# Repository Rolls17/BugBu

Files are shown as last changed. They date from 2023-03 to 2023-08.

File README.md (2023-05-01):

# BugBu
Budget Bambu Lab P1P style printer, hence, BugBu. 

Print parts as oriented.  Part description will tell you quantity and if supports are needed.  All parts designed for 0.2mm layer height, 6 walls minimum recommended for strength.

Discord:  https://discord.gg/kHFhCXZnxb

Preview:  https://www.youtube.com/watch?v=aXq7XMQ8wdc

Introduction:  https://www.youtube.com/watch?v=87gVqnMzinw

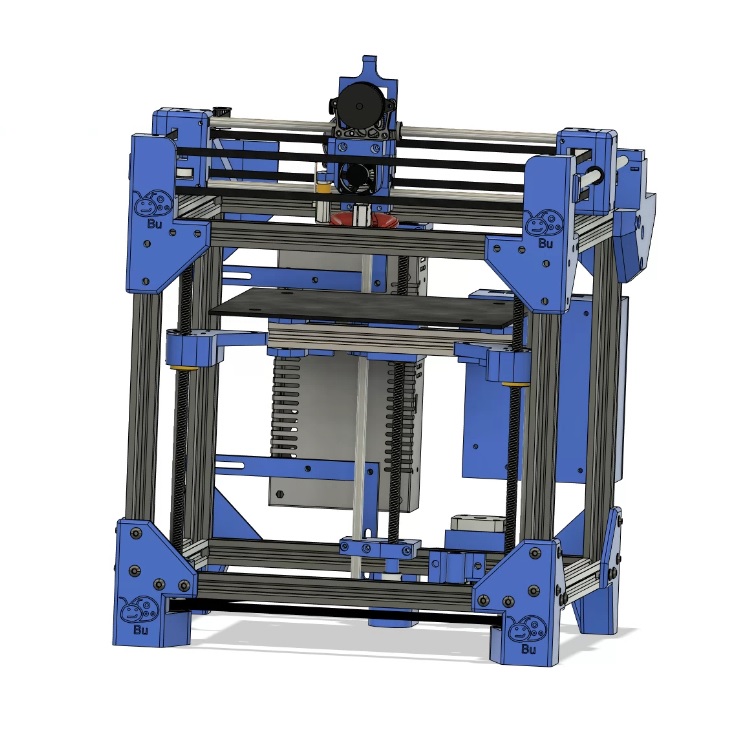
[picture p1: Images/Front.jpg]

Alt text BugBu © 2023 by Royce Rentz is licensed under CC BY-NC 4.0. To view a copy of this license, visit http://creativecommons.org/licenses/by-nc/4.0/

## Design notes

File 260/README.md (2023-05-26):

The BugBu 260 has a printable area of 235x235x300 unless you slap on a Bambu build plate, then you get 260x250x300 build volume.  This uses a cantilever bed to eliminate the closed loop belt system.  All part are printed at 6 walls and 20% infill minimum, designed for 0.4 nozzle at 0.2 layer height.  With lots of testing hours, it is working well currently on the cantilever, but there will be mods coming for it to give a couple of bed operation options.

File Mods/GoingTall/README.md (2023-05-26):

This mod is ONLY for the 310 version of the BugBu. Just replace the same
name parts from the BugBu 310 list with these parts to go tall. You will also
need 2 - MGN12 linear rails for this mod. The linear rails will need to be
50mm shorter than the extrusions you are using for height. For example: If
you order 4 - 500mm extrusions for the height, you would need 2 mgn12
at 450mm. You will also need to use more braces, and be sure your bug is
secured to the table or bench it is on, is it will be top heavy with this mod.
Additional Parts Needed/Deleted from 310 BOM:
ADD - 2 EA: MGN12 linear rails. These will replace 2 linear rods, but you
will still need 1 Linear rod the same length as your Z extrusions. The
MGN12 will need to be 50mm Shorter as noted above
DELETE - 2 EA: Linear Rods for the Z and Linear Bearings for the Z
All other parts in the 310 BOM will remain the same.

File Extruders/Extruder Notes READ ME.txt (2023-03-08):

My current design is standard for the Sherpa Mini mount.  The following are the extruder I can confirm work with the printer.

Sherpa Mini: https://github.com/Annex-Engineering/Sherpa_Mini-Extruder
Print the STL's within the github and follow assembly instructions

Vorxtrudort:  https://github.com/nhchiu/VoronMods/tree/main/Extruders/Vorxtrudort
Print the STL's within the github, BE SURE to print the Sherpa Mini Friction Fit body.  Follow assembly instruction on the github

Hummingbird:  https://github.com/nhchiu/VoronMods/tree/main/Extruders/Hummingbird
Print the STL's within the github, you will also need to order the big gear kit from Aliexpress that is linked in the github.  To mount the Hummingbird, there is an adapter plate STL in the Extruder folder on my page that will mount the extruder.  Follow the assembly instruction on the github.

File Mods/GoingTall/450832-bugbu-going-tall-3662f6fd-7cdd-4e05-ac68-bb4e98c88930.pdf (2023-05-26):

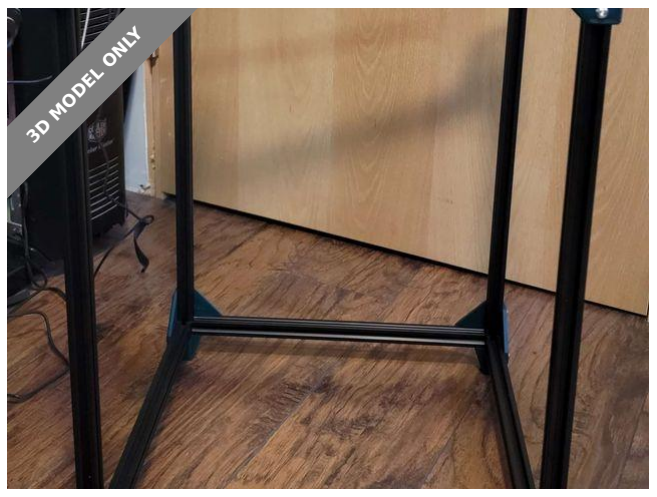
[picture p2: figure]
3D MODEL ONLY

## Summary

This is a mod to allow users to grow the BugBu in height without compromising Z stability

3D Printers (https://printables.com/model?categoryId=1) > 3D Printers - Upgrades (https://printables.com/model?categoryId=2)

Tags: bambu | bugbu | bugbu310 | bugbugoingtall | tallbugbu

This mod is ONLY for the 310 version of the BugBu. Just replace the same name parts from the BugBu 310 list with these parts to go tall. You will also need 2 - MGN12 linear rails for this mod. The linear rails will need to be 50mm shorter than the extrusions you are using for height. For example: If you order 4 - 500mm extrusions for the height, you would need 2 mgn12 at 450mm. You will also need to use more braces, and be sure your bug is secured to the table or bench it is on, is it will be top heavy with this mod.

Additional Parts Needed/Deleted from 310 BOM:

ADD - 2 EA: MGN12 linear rails. These will replace 2 linear rods, but you will still need 1 Linear rod the same length as your Z extrusions. The MGN12 will need to be 50mm Shorter as noted above

DELETE - 2 EA: Linear Rods for the Z and Linear Bearings for the Z

All other parts in the 310 BOM will remain the same.

Rolls17 (https://printables.com/@Rolls17_586768)

## BugBu Going Tall

VIEW IN BROWSER (https://printables.com/model/450832-bugbu-going-tall)

updated 12. 5. 2023 | published 12. 5. 2023

## Model files

fr_bottom_frame_x1.stl

fr_top_x1.stl

fr_bottom_clamp_x1.stl

fl_top_x1.stl

fl_bottom_clamp_x1.stl

fr_top_frame_x1.stl

fl_top_frame_x1.stl

fl_bottom_frame_x1.stl

foot_fr_for_tall_x1.stl

## License

This work is licensed under a
Creative Commons (4.0 International License)

Attribution-NonCommercial (http://creativecommons.org/licenses/by-nc/4.0/)

✖ | Sharing without ATTRIBUTION
✔ | Remix Culture allowed
✖ | Commercial Use
✖ | Free Cultural Works
✖ | Meets Open Definition

idler_fr_for_tall_x1.stl

foot_fl_for_tall_x1.stl

idler_fl_for_tall_x1.stl

310-back-bed-mount-x2-for-using-springs-print-with-… .stl

fr-z-to-bed-for-tall-x1-v1.stl

fl-z-to-bed-for-tall-x1-v1.stl

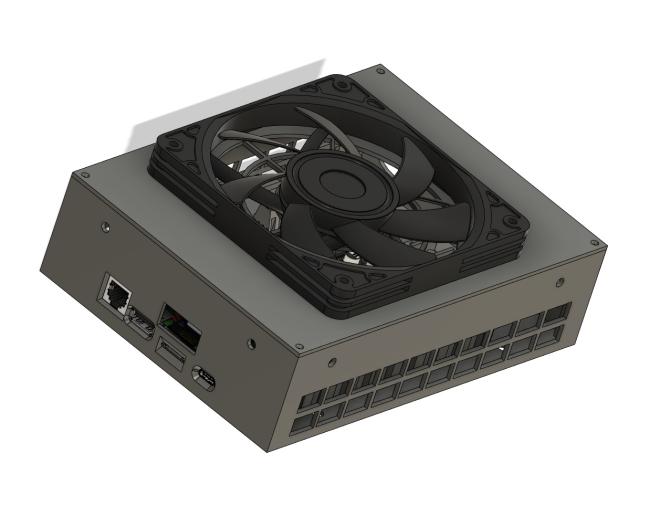
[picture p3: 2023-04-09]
STL Files/Electronics/Octopus/Octopus_Backpack.jpg

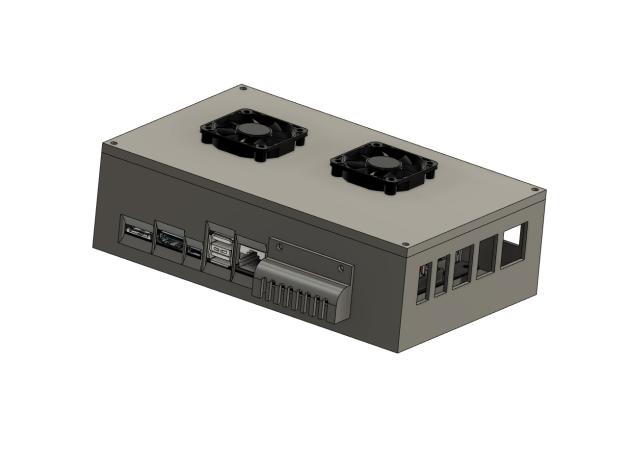
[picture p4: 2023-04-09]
STL Files/Electronics/Manta_M4P/Manta_M4P_Backpack.jpg

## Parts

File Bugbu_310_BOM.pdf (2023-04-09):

MOTION: | Quantity | Price Each | Total | Amazon or Ali Link to Suggested Part
GT2 6mm Belt, 5 meter minimum length | 1 | $9.00 | $9.00
| | | | https://www.amazon.com/dp/B097T212B9/ref=twister_B09877BH12?_e ncoding=UTF8&psc=1
GT2 20 Toothless 5mm bore idler | 10 | $1.20 | $12.00 Printer/dp/B07RV2T54M/ref=sr_1_3?crid=OFZKSAD0WYW1&keywords=g
GT2 20 Tooth 5mm bore timing pulley | 2 | $4.50 | $9.00

https://www.amazon.com/WINSINN-Aluminum-Timing-Pulley-Printer/dp/B07BPGYX3G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

GT2 20 Tooth 5mm bore stepper timing pulley | 3 | $2.50 | $7.50

https://www.amazon.com/WINSINN-Aluminum-Synchronous-Timing-Printer/dp/B077GNZK3J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

GT2 20 Tooth 8mm bore pulley | 3 | $2.50 | $7.50

https://www.amazon.com/WINSINN-Aluminum-Synchronous-Timing-Printer/dp/B077GMKW1C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

8mm linear rod 400mm | 7 | $7.00 | $49.00

https://www.amazon.com/Linear-Motion-15-748-Hardened-Printer/dp/B08JGD9F5P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

### BugBu 310 BOM (315x300x300 build volume)

Please note: The items listed don't include any extra wiring or a Pi and as with any BOM, there are going to be small miscellaneous parts needed along the way. The scew assortments will hopefully cover a lot of the miscellaneous. For a more rigid gantry, 4 - 45mm Linear Bearings are better, but the shorter ones in the BOM will work fine. This list is only a guide, better pricing may be found elsewhere. While every effort has been made to make this a complete list, and the design easy to assemble, please know this is still a self sourced ground up 3D printer build and will require printed parts, time, and attention to details. All work is done so at your own risk and without any liability to the designer of the project.

The STL file parts are pre orientated for best printing. Print with no less than 6 walls and 20% infill. The STL file name will tell you quantity of each item and if it needs supports, only two parts should need supports. I use Polymaker PLA Pro for the parts unless I enclose the printer, I go to Polymaker ASA or ABS.

Linear Bearings | 10 | $1.00 | $10.00

https://www.amazon.com/LM8UU-Linear-Bearings-Length-Printer/dp/B087WPGQ8T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
spons&psc=1&spLa=ZW5jcnlwdGVkUXVhbGlmaWVyPUEyTjRCSDI0RUNW UjZRJmVuY3J5cHRlZElkPUEwODkyMjYwM0ZZOFVJNkFKUVhLOSZlbmNyeX B0ZWRBZElkPUEwMDMxNjg1MVQxUFVBMTRGRVFaTCZ3aWRnZXROYW1 lPXNwX2F0ZiZhY3Rpb249Y2xpY2tSZWRpcmVjdCZkb05vdExvZ0NsaWNrPX RydWU=
Nema17 42mm stepper motor | 3 | $8.25 | $24.75

https://www.amazon.com/POLISI3D-Printer-Stepper-Stepping-Connector/dp/B08HWGYY9D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

8mm 4-start lead screw 400mm | 3 | $11.00 | $33.00

https://www.amazon.com/400mm%EF%BC%8815-75-Inches%EF%BC%89Tr8x8-Thread-Printer-Machine/dp/B08JPNMWP8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

Closed Loop GT2 6mm belt, 1434mm | 1 | $7.00 | $7.00

https://www.aliexpress.us/item/2251832627424600.html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

608 Bearings 8x22x7 skateboard bearings | 9 | $0.56 | $5.04 https://www.amazon.com/%EF%BC%BB10-Pack%EF%BC%BD-608-Ball-
| | | Bearings/dp/B08XVFSZTF/ref=sr_1_4?crid=1QS8OGIPNR2RK&keywords=6
| | | 08+bearing&qid=1677779566&s=industrial&sprefix=608+bearing%2Cindu
| | | strial%2C174&sr=1-4
| | | $0.00
HARDWARE | | | $0.00
Full fastener cart from Bolt Depot
NOTE: Add all items on the list to your cart. This should be all the fasteners you need ACCEPT the t-
nuts. T-nuts listed below. | 1 | $35.00 | $35.00 https://www.boltdepot.com/cart/208641
M5 T-slot/T-nut (this link is for the twist style, there
is a link below in alternates for spring loaded. Pick
your preference) | 100 | $0.06 | $6.00 https://www.amazon.com/Hulless-Sliding-Fastener-Aluminum-
| | | Accessories/dp/B08NZMVP6N/ref=sr_1_14?keywords=m5+t+nut&qid=16
| | | 76582188&sprefix=m5+t%2Caps%2C237&sr=8-14

2020 aluminum extrusion 400mm 10 pack (t or v slot)
You will need a 10 pack and 4 pack, 12 pieces for
the frame and 1 for the print bed (print bed piece
can be left 400 or cut to 300) | 10 | $4.00 | $40.00 https://www.amazon.com/Aluminum-Extrusion-European-Standard-
| | | Industrial/dp/B0B2P434PD/ref=sr_1_8?crid=2H8WDJUWS4H8K&keyword
| | | s=2020%2Baluminum%2Bextrusion%2B300mm&qid=1676582392&sprefix
| | | =2020%2Baluminum%2Bextrusion%2B300mm%2Caps%2C154&sr=8-
| | | 8&th=1

2020 aluminum extrusion 400mm 4 pack(t or v slot) | 4 | $4.75 | $19.00

https://www.amazon.com/OUYZGIA-Aluminum-Extrusion-Extruded-Building/dp/B0B2N3F8DS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

| | | $0.00

EXTRUDER: Note that my design can accommodate a few designs, select which one you want to use, just note you will need a different gear kit for the
Hummbingbird Extruder | | | $0.00
BMG dual drive extruder kit | 1 | $18.00 | $18.00

https://www.amazon.com/Precision-Printer-Plating-Hardened-Extruder/dp/B097YL3C6J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

3D Printed Sherpa Mini (Print parts and assemble)
Use the STL's and build instructions from the GitHub | 1 | https://github.com/Annex-Engineering/Sherpa_Mini-Extruder

3D Printed Hummingbird (Print parts and assemble.
Order big gear kit from Github link) Use the STL's
and build instructions from the GitHub https://github.com/nhchiu/VoronMods/tree/main/Extruders/Hummingbi rd
| | | $0.00
HEATED BED | | | $0.00
Standard ender CR-10 310x310 24v bed | 1 | $42.00 | $42.00

https://www.amazon.com/310x310mm-Aluminum-HeatBed-Thickness-Creality/dp/B07H8DXVQD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

310x310 Build Sheet | 1 | $26.00 | $26.00

https://www.amazon.com/dp/B09M3N2FVS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
| | | $0.00
ELECTRONICS | | | $0.00
3D Touch | 1 | $16.00 | $16.00

https://www.amazon.com/3Dman-Upgrade-Leveling-Sensor-Printers/dp/B08SK62RMR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

24v Power Supply | 1 | $24.00 | $24.00

https://www.amazon.com/ALITOVE-Universal-Regulated-Switching-Transformer/dp/B06XK2ZNKC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 prefix=24v+%2Caps%2C461&sr=1-1-5985efba-8948-4f09-9122-d605505c9d1e

BTT E3 V2/V3 or MKS Robin E3 v1.1 | 1 | $40.00 | $40.00

https://www.amazon.com/BIGTREETECH-Upgrade-Control-TMC2209-Creality/dp/B0882QGFZR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
spons&psc=1&spLa=ZW5jcnlwdGVkUXVhbGlmaWVyPUFQWDA4RVRFNFh GR00mZW5jcnlwdGVkSWQ9QTAwMTk0OTROOFdVWVhEWDdBRjcmZW5 jcnlwdGVkQWRJZD1BMDA2MjM2MTFLUVE1UzUwVU5GUlMmd2lkZ2V0T mFtZT1zcF9hdGYmYWN0aW9uPWNsaWNrUmVkaXJlY3QmZG9Ob3RMb2 dDbGljaz10cnVl
Triangle-lab CHC hotend
The link gives you the option of either standard or
volcano for $5 more, the volcano is recommended
over the standard | 1 | $35.00 | $35.00

https://west3d.com/products/chc-ceramic-heater-core-hot-end-kit-v6-and-volcano-variants-pro

Nema 14 Pancake Stepper | 1 | $22.00 | $22.00

https://www.amazon.com/FYSETC-Printer-Extruder-47-2inch-Accessories/dp/B099JMJNH2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

3010 24v Fan | 1 | $9.00 | $9.00

https://www.amazon.com/HKWANTAT-Bearings-Brushless-Cooling-30x30x10mm/dp/B09MCJ2XSP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

5015 24v Fan | 1 | $9.00 | $9.00

https://www.amazon.com/Brushless-Hydraulic-50mmx50mmx15mm-Appliances-Replacement/dp/B0BBZPB4DM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

Fan wire extensions | 2 | $5.50 | $11.00

https://www.amazon.com/REIFENG-Printer-Cooling-Extension-Connection/dp/B09BN5X6ZT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

Power Switch | 1 | $8.00 | $8.00

https://www.amazon.com/dp/B07KS2TQ45?ref=ppx_yo2ov_dt_b_product_details&th=1
| | | $533.79

## Alternate parts and upgrades

Spring Loaded t-nuts

https://www.amazon.com/Rierdge-European-Standard-Aluminum-Extrusion/dp/B09B3H8RJP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

Pre-assembled Sherpa Mini with stepper motor https://www.amazon.com/FYSETC-Sherpa-Extruder-Compatible-Printer/dp/B095WFBGL4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

BTT BLTouch

https://www.amazon.com/BIGTREETECH-BLTouch-Leveling-Extension-Upgrade/dp/B087CQ3RLG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

Creality CRTouch

https://www.amazon.com/gp/product/B09XCGPLXH/ref=ewc_pr_img_1?smid=A113EI13J39RO4&psc=1

## Individual fastener list in case you need to source from elsewhere

M3, M4, M5 Nut and Screw Kit | 1 | $15.00

https://www.amazon.com/Hilitchi-510-Pcs-Socket-Screws-Assortment/dp/B073SWXPYR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
0186dd22447b&pd_rd_w=jmPHz&pd_rd_wg=kQ31h&pf_rd_p=8f2bf95d-b9c2-4e6d-96a9-
5fdf77a1951d&pf_rd_r=RBMRTG4MGTVCWFG3QMHH&qid=1677710013 &sprefix=M3+M4+M%2Caps%2C158&sr=1-1-270ce31b-afa8-499f-878b-3bb461a9a5a6
M3 longer fastener kit | 1 | $9.28

https://www.amazon.com/iexcell-Metric-M5-0-8-Stainless-Assortment/dp/B08GZWVN4D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

M5 longer fastener kit | 1 | $9.80

https://www.amazon.com/iexcell-Metric-M5-0-8-Stainless-Assortment/dp/B07HDL3KVG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

Assorted M3 Kit | 1 | $12.00

https://www.amazon.com/Kadrick-Bolts%EF%BC%8CFlat-Washers-Assortment-Stainless/dp/B0BPFWBBF9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 N00mZW5jcnlwdGVkSWQ9QTA0MzU1MDgzSVdTSUdRRlQ2NVBOJmVuY3 J5cHRlZEFkSWQ9QTAwMjM5ODcxT0pGTURMRUdQSUZXJndpZGdldE5hb WU9c3BfYXRmJmFjdGlvbj1jbGlja1JlZGlyZWN0JmRvTm90TG9nQ2xpY2s9d HJ1ZQ==

M4x50 countersunk flat head | 4 | $2.00

https://www.amazon.com/METALLIXITY-Countersunk-Machine-M4x30mm-Stainless/dp/B09Y5P7X75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

M5x12 (M5x10 works too) button head | 100 | $0.10

https://www.amazon.com/M5-0-8-Button-Socket-Stainless-Quantity/dp/B07NVJT9VB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 R0tNJmVuY3J5cHRlZElkPUEwNjE3MjQyNFBaWERJNkJaNFZCJmVuY3J5cHR lZEFkSWQ9QTAxMTk0NzMxTjlKWDg1SDVHN1NaJndpZGdldE5hbWU9c3Bf YXRmJmFjdGlvbj1jbGlja1JlZGlyZWN0JmRvTm90TG9nQ2xpY2s9dHJ1ZQ==

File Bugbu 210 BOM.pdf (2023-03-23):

MOTION: | Quantity | Price Each | Total | Amazon or Ali Link to Suggested Part
GT2 6mm Belt, 5 meter minimum length | 1 | $9.00 | $9.00
| | | | https://www.amazon.com/dp/B097T212B9/ref=twister_B09877BH12?_e ncoding=UTF8&psc=1
GT2 20 Toothless 5mm bore idler | 10 | $1.20 | $12.00 Printer/dp/B07RV2T54M/ref=sr_1_3?crid=OFZKSAD0WYW1&keywords=g
GT2 20 Tooth 5mm bore timing pulley | 2 | $4.50 | $9.00

https://www.amazon.com/WINSINN-Aluminum-Timing-Pulley-Printer/dp/B07BPGYX3G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

GT2 20 Tooth 5mm bore stepper timing pulley | 3 | $2.50 | $7.50

https://www.amazon.com/WINSINN-Aluminum-Synchronous-Timing-Printer/dp/B077GNZK3J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

GT2 20 Tooth 8mm bore pulley | 3 | $2.50 | $7.50

https://www.amazon.com/WINSINN-Aluminum-Synchronous-Timing-Printer/dp/B077GMKW1C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

8mm linear rod 300mm | 7 | $5.25 | $36.75

https://www.amazon.com/300mm-Linear-Motion-Printer-Machine/dp/B09P87MSY7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

### BugBu 300 BOM (215x200x200 build volume)

Please note: The items listed don't include any extra wiring or a Pi and as with any BOM, there are going to be small miscellaneous parts needed along the way. The scew assortments will hopefully cover a lot of the miscellaneous. For a more rigid gantry, 4 - 45mm Linear Bearings are better, but the shorter ones in the BOM will work fine. This list is only a guide, better pricing may be found elsewhere. While every effort has been made to make this a complete list, and the design easy to assemble, please know this is still a self sourced ground up 3D printer build and will require printed parts, time, and attention to details. All work is done so at your own risk and without any liability to the designer of the project.

The STL file parts are pre orientated for best printing. Print with no less than 6 walls and 20% infill. The STL file name will tell you quantity of each item and if it needs supports, only two parts should need supports. I use Polymaker PLA Pro for the parts unless I enclose the printer, I go to Polymaker ASA or ABS.

Linear Bearings | 10 | $1.00 | $10.00

https://www.amazon.com/LM8UU-Linear-Bearings-Length-Printer/dp/B087WPGQ8T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
spons&psc=1&spLa=ZW5jcnlwdGVkUXVhbGlmaWVyPUEyTjRCSDI0RUNW UjZRJmVuY3J5cHRlZElkPUEwODkyMjYwM0ZZOFVJNkFKUVhLOSZlbmNyeX B0ZWRBZElkPUEwMDMxNjg1MVQxUFVBMTRGRVFaTCZ3aWRnZXROYW1 lPXNwX2F0ZiZhY3Rpb249Y2xpY2tSZWRpcmVjdCZkb05vdExvZ0NsaWNrPX RydWU=
Nema17 42mm stepper motor | 3 | $8.25 | $24.75

https://www.amazon.com/POLISI3D-Printer-Stepper-Stepping-Connector/dp/B08HWGYY9D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

8mm 4-start lead screw 300mm | 3 | $7.00 | $21.00

https://www.amazon.com/ReliaBot-300mm-Thread-Starts-Printer/dp/B0829J9YJ1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

Closed Loop GT2 6mm belt, 1080mm - 1100mm | 1 | $6.50 | $6.50

https://www.aliexpress.us/item/2251832113069399.html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 bd8be16777098448855150d06df%2110000003969762805%21sea%21US %210&curPageLogUid=Sgd0cwKojbJx

608 Bearings 8x22x7 skateboard bearings | 9 | $0.56 | $5.04

https://www.amazon.com/%EF%BC%BB10-Pack%EF%BC%BD-608-Ball-Bearings/dp/B08XVFSZTF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
| | | $0.00
HARDWARE | | | $0.00
M5x12 (M5x10 works too) button head | 100 | $0.10 | $10.00

https://www.amazon.com/M5-0-8-Button-Socket-Stainless-Quantity/dp/B07NVJT9VB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 R0tNJmVuY3J5cHRlZElkPUEwNjE3MjQyNFBaWERJNkJaNFZCJmVuY3J5cHR lZEFkSWQ9QTAxMTk0NzMxTjlKWDg1SDVHN1NaJndpZGdldE5hbWU9c3Bf YXRmJmFjdGlvbj1jbGlja1JlZGlyZWN0JmRvTm90TG9nQ2xpY2s9dHJ1ZQ==

M5 T-slot/T-nut | 100 | $0.06 | $6.00

https://www.amazon.com/Hulless-Sliding-Fastener-Aluminum-Accessories/dp/B08NZMVP6N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

Assorted M3 Kit | 1 | $12.00 | $12.00

https://www.amazon.com/Kadrick-Bolts%EF%BC%8CFlat-Washers-Assortment-Stainless/dp/B0BPFWBBF9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 N00mZW5jcnlwdGVkSWQ9QTA0MzU1MDgzSVdTSUdRRlQ2NVBOJmVuY3 J5cHRlZEFkSWQ9QTAwMjM5ODcxT0pGTURMRUdQSUZXJndpZGdldE5hb WU9c3BfYXRmJmFjdGlvbj1jbGlja1JlZGlyZWN0JmRvTm90TG9nQ2xpY2s9d HJ1ZQ==

M4x50 countersunk flat head | 4 | $2.00 | $8.00

https://www.amazon.com/METALLIXITY-Countersunk-Machine-M4x30mm-Stainless/dp/B09Y5P7X75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
2020 aluminum extrusion 300mm 10 pack (t or v slot)
You will need a 10 pack and 4 pack, 12 pieces for
the frame and 1 for the print bed (print bed piece
can be left 300 or cut to 200) | 10 | $3.25 | $32.50

https://www.amazon.com/Aluminum-Extrusion-European-Standard-Industrial/dp/B0B2PBF6YB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

2020 aluminum extrusion 300mm 4 pack(t or v slot) | 4 | $4.00 | $16.00

https://www.amazon.com/OUYZGIA-Aluminum-Extrusion-Extruded-Building/dp/B0B2N4YY1W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

M3, M4, M5 Nut and Screw Kit | 1 | $15.00 | $15.00

https://www.amazon.com/Hilitchi-510-Pcs-Socket-Screws-Assortment/dp/B073SWXPYR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
0186dd22447b&pd_rd_w=jmPHz&pd_rd_wg=kQ31h&pf_rd_p=8f2bf95d-b9c2-4e6d-96a9-
5fdf77a1951d&pf_rd_r=RBMRTG4MGTVCWFG3QMHH&qid=1677710013 &sprefix=M3+M4+M%2Caps%2C158&sr=1-1-270ce31b-afa8-499f-878b-3bb461a9a5a6

M3 longer fastener kit | 1 | $9.28 | $9.28

https://www.amazon.com/iexcell-Metric-M5-0-8-Stainless-Assortment/dp/B08GZWVN4D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

M5 longer fastener kit | 1 | $9.80 | $9.80

https://www.amazon.com/iexcell-Metric-M5-0-8-Stainless-Assortment/dp/B07HDL3KVG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
| | | $0.00

EXTRUDER: Note that my design can accommodate a few designs, select which one you want to use, just note you will need a different gear kit for the
Hummbingbird Extruder | | | $0.00
BMG dual drive extruder kit | 1 | $18.00 | $18.00

https://www.amazon.com/Precision-Printer-Plating-Hardened-Extruder/dp/B097YL3C6J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

3D Printed Sherpa Mini (Print parts and assemble)
Use the STL's and build instructions from the GitHub | 1 | https://github.com/Annex-Engineering/Sherpa_Mini-Extruder

3D Printed Vorxtrudort (Print parts and assemble)
Use the STL's and build instructions from the GitHub | https://github.com/nhchiu/VoronMods/tree/main/Extruders/Vorxtrudort

3D Printed Hummingbird (Print parts and assemble.
Order big gear kit from Github link) Use the STL's
and build instructions from the GitHub https://github.com/nhchiu/VoronMods/tree/main/Extruders/Hummingbi rd
| | | $0.00
HEATED BED | | | $0.00
Standard ender 3 235x235 24v bed | 1 | $25.00 | $25.00

https://www.amazon.com/Ender-V2-Heated-Bed-Replacement/dp/B08VHTW8CQ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
spons&psc=1&spLa=ZW5jcnlwdGVkUXVhbGlmaWVyPUExQjRXTFBEVzlON 0ZIJmVuY3J5cHRlZElkPUEwODY2MjI3MjhIVkxDODZEUUk4UyZlbmNyeXB0 ZWRBZElkPUEwMzMxNDM0M1RBNkM2UDRIV01IWCZ3aWRnZXROYW1lP XNwX2F0ZiZhY3Rpb249Y2xpY2tSZWRpcmVjdCZkb05vdExvZ0NsaWNrPXRy dWU=

235x235 build sheet | 1 | $12.00 | $12.00

https://www.amazon.com/dp/B0856VT5XT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
| | | $0.00
ELECTRONICS | | | $0.00
3D Touch | 1 | $16.00 | $16.00

https://www.amazon.com/3Dman-Upgrade-Leveling-Sensor-Printers/dp/B08SK62RMR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

24v Power Supply | 1 | $24.00 | $24.00

https://www.amazon.com/ALITOVE-Universal-Regulated-Switching-Transformer/dp/B06XK2ZNKC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 prefix=24v+%2Caps%2C461&sr=1-1-5985efba-8948-4f09-9122-d605505c9d1e

BTT E3 V2/V3 or MKS Robin E3 v1.1 | 1 | $40.00 | $40.00

https://www.amazon.com/BIGTREETECH-Upgrade-Control-TMC2209-Creality/dp/B0882QGFZR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
spons&psc=1&spLa=ZW5jcnlwdGVkUXVhbGlmaWVyPUFQWDA4RVRFNFh GR00mZW5jcnlwdGVkSWQ9QTAwMTk0OTROOFdVWVhEWDdBRjcmZW5 jcnlwdGVkQWRJZD1BMDA2MjM2MTFLUVE1UzUwVU5GUlMmd2lkZ2V0T mFtZT1zcF9hdGYmYWN0aW9uPWNsaWNrUmVkaXJlY3QmZG9Ob3RMb2 dDbGljaz10cnVl

Triangle-lab CHC hotend | 1 | $31.00 | $31.00

https://www.aliexpress.us/item/3256803662839179.html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 00bb6416777106954414139d0729%2112000027332429742%21sea%21U S%210&curPageLogUid=cpJxAMdvL2Ar

Nema 14 Pancake Stepper | 1 | $22.00 | $22.00

https://www.amazon.com/FYSETC-Printer-Extruder-47-2inch-Accessories/dp/B099JMJNH2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

3010 24v Fan | 1 | $9.00 | $9.00

https://www.amazon.com/HKWANTAT-Bearings-Brushless-Cooling-30x30x10mm/dp/B09MCJ2XSP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

5015 24v Fan | 1 | $9.00 | $9.00

https://www.amazon.com/Brushless-Hydraulic-50mmx50mmx15mm-Appliances-Replacement/dp/B0BBZPB4DM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

Power Switch | 1 | $8.00 | $8.00

https://www.amazon.com/dp/B07KS2TQ45?ref=ppx_yo2ov_dt_b_product_details&th=1
| | | $481.62

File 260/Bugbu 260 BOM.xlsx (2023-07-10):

BugBu 260 BOM (Acheivable 260x250x300 build volume) This build uses the Ender 3 24v Heated Bed. You can either use the full 235x235 bed area with space around it, or get a Bambu build plate to get a 260x250 print bed area
Please note: The items listed don't include any extra wiring or a Pi and as with any BOM, there are going to be small miscellaneous parts needed along the way. The scew assortments will hopefully cover a lot of the miscellaneous. For a more rigid gantry, 4 - 45mm Linear Bearings are better, but the shorter ones in the BOM will work fine. This list is only a guide, better pricing may be found elsewhere. While every effort has been made to make this a complete list, and the design easy to assemble, please know this is still a self sourced ground up 3D printer build and will require printed parts, time, and attention to details. All work is done so at your own risk and without any liability to the designer of the project. The STL file parts are pre orientated for best printing. Print with no less than 6 walls and 20% infill. The STL file name will tell you quantity of each item and if it needs supports, only two parts should need supports. I use Polymaker PLA Pro for the parts unless I enclose the printer, I go to Polymaker ASA or ABS.
MOTION: | Quantity | Price Each | Total | Amazon or Ali Link to Suggested Part
GT2 6mm Belt, 5 meter minimum length | 1 | $9.00 | $9.00 | https://www.amazon.com/dp/B097T212B9/ref=twister_B09877BH12?_encoding=UTF8&psc=1
GT2 20 Toothless 5mm bore idler | 7 | $1.75 | $12.25 | https://www.amazon.com/3Dman-Toothless-Aluminum-Timing-Printer/dp/B07RV2T54M
GT2 20 Tooth 5mm bore timing pulley | 2 | $4.50 | $9.00 | https://www.amazon.com/WINSINN-Aluminum-Timing-Pulley-Printer/dp/B07BPGYX3G
GT2 20 Tooth 5mm bore stepper timing pulley | 3 | $2.50 | $7.50 | https://www.amazon.com/WINSINN-Aluminum-Synchronous-Timing-Printer/dp/B077GNZK3J
8mm linear rod 350mm | 4 | $4.50 | $18.00 | https://www.amazon.com/300mm-Linear-Motion-Printer-Machine/dp/B09P86HCNM
Linear Bearings (these are 45mm bearings and much smoother than the cheap 10 pack) | 4 | $4.00 | $16.00 | https://www.amazon.com/Printer-Bearings-JGAurora-LM08LUU-LM8LUU/dp/B083XQTH41
Nema17 42mm stepper motor | 3 | $8.25 | $24.75 | https://www.amazon.com/POLISI3D-Printer-Stepper-Stepping-Connector/dp/B08HWGYY9D
8mm 4-start lead screw 350mm | 1 | $9.50 | $9.50 | https://www.amazon.com/ReliaBot-300mm-Thread-Starts-Printer/dp/B078R7XJP3
MGN12H Linear Rail | 2 | $19.00 | $38.00 | https://www.amazon.com/dp/B0B1LZBXXL?ref=ppx_yo2ov_dt_b_product_details&th=1
5mm to 8mm coupler | 1 | $6.49 | $6.49 | https://www.amazon.com/uxcell-Coupling-Aluminum-Connector-Accessories/dp/B08HCKXGQD
 |  |  | $0.00
HARDWARE |  |  | $0.00
Full fastener cart from Bolt Depot NOTE: Add all items on the list to your cart. This should be all the fasteners you need ACCEPT the t-nuts. T-nuts listed below. | 1 | $35.00 | $35.00 | https://www.boltdepot.com/cart/208641
M5 T-slot/T-nut (this link is for the twist style, there is a link below in alternates for spring loaded. Pick your preference) | 100 | $0.06 | $6.00 | https://www.amazon.com/Hulless-Sliding-Fastener-Aluminum-Accessories/dp/B08NZMVP6N
2019 aluminum extrusion 350mm (t or v slot) | 8 | $4.75 | $38.00 | https://www.amazon.com/BELLA-BAYS-Extrusion-20mmx20mm-Engraving/dp/B08TBL625V?s=industrial
2020 aluminum extrusion 400mm (t or v slot) | 4 | $5.00 | $20.00 | https://www.amazon.com/BELLA-BAYS-Extrusion-20mmx20mm-Engraving/dp/B08TBL5V61?s=industrial
2021 aluminum extrusion 300mm (t or v slot) | 2 | $6.00 | $12.00 | https://www.amazon.com/BELLA-BAYS-Extrusion-20mmx20mm-Engraving/dp/B08TBHFWK3?s=industrial
 |  |  | $0.00
EXTRUDER: Note that my design can accommodate a few designs, select which one you want to use, just note you will need a different gear kit for the Hummbingbird Extruder |  |  | $0.00
BMG dual drive extruder kit | 1 | $18.00 | $18.00 | https://www.amazon.com/Precision-Printer-Plating-Hardened-Extruder/dp/B097YL3C6J
3D Printed Sherpa Mini (Print parts and assemble) Use the STL's and build instructions from the GitHub | 1 |  |  | https://github.com/Annex-Engineering/Sherpa_Mini-Extruder
3D Printed Vorxtrudort (Print parts and assemble) Use the STL's and build instructions from the GitHub |  |  |  | https://github.com/nhchiu/VoronMods/tree/main/Extruders/Vorxtrudort
3D Printed Hummingbird (Print parts and assemble. Order big gear kit from Github link) Use the STL's and build instructions from the GitHub |  |  |  | https://github.com/nhchiu/VoronMods/tree/main/Extruders/Hummingbird
 |  |  | $0.00
HEATED BED |  |  | $0.00
Standard ender 3 235x235 24v bed | 1 | $25.00 | $25.00 | https://www.amazon.com/Ender-V2-Heated-Bed-Replacement/dp/B08VHTW8CQ
235x235 build sheet | 1 | $12.00 | $12.00 | https://www.amazon.com/dp/B0856VT5XT
 |  |  | $0.00
ELECTRONICS |  |  | $0.00
3D Touch | 1 | $16.00 | $16.00 | https://www.amazon.com/3Dman-Upgrade-Leveling-Sensor-Printers/dp/B08SK62RMR
24v Power Supply | 1 | $24.00 | $24.00 | https://www.amazon.com/ALITOVE-Universal-Regulated-Switching-Transformer/dp/B06XK2ZNKC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
BTT E3 V2/V3 or MKS Robin E3 v1.1 | 1 | $40.00 | $40.00 | https://www.amazon.com/BIGTREETECH-Upgrade-Control-TMC2209-Creality/dp/B0882QGFZR
Triangle-lab CHC hotend The link gives you the option of either standard or volcano for $5 more, the volcano is recommended over the standard | 1 | $35.00 | $35.00 | https://west3d.com/products/chc-ceramic-heater-core-hot-end-kit-v6-and-volcano-variants-pro
Nema 14 Pancake Stepper | 1 | $22.00 | $22.00 | https://www.amazon.com/FYSETC-Printer-Extruder-47-2inch-Accessories/dp/B099JMJNH2
3010 24v Fan | 1 | $9.00 | $9.00 | https://www.amazon.com/HKWANTAT-Bearings-Brushless-Cooling-30x30x10mm/dp/B09MCJ2XSP
5015 24v Fan | 1 | $9.00 | $9.00 | https://www.amazon.com/Brushless-Hydraulic-50mmx50mmx15mm-Appliances-Replacement/dp/B0BBZPB4DM
Fan wire extensions | 2 | $5.50 | $11.00 | https://www.amazon.com/REIFENG-Printer-Cooling-Extension-Connection/dp/B09BN5X6ZT
Power Switch | 1 | $8.00 | $8.00 | https://www.amazon.com/dp/B07KS2TQ45?ref=ppx_yo2ov_dt_b_product_details&th=1
 |  |  | $490.49
Alternate parts and upgrades
Spring Loaded t-nuts |  |  |  | https://www.amazon.com/Rierdge-European-Standard-Aluminum-Extrusion/dp/B09B3H8RJP
Pre-assembled Sherpa Mini with stepper motor |  |  |  | https://www.amazon.com/FYSETC-Sherpa-Extruder-Compatible-Printer/dp/B095WFBGL4
BTT BLTouch |  |  |  | https://www.amazon.com/BIGTREETECH-BLTouch-Leveling-Extension-Upgrade/dp/B087CQ3RLG
Creality CRTouch |  |  |  | https://www.amazon.com/gp/product/B09XCGPLXH/ref=ewc_pr_img_1?smid=A113EI13J39RO4&psc=1
Metal inside corners for strength (will need more M5x12 or 10 and tnuts for these) |  |  |  | https://www.amazon.com/dp/B07P9GBNNQ?ref=ppx_yo2ov_dt_b_product_details&th=1
Metal antibacklash nut (or us POM if you prefer) | 1 |  |  | https://www.amazon.com/ReliaBot-Backlash-Spring-Elimination-Threaded/dp/B079JQ7S3Y
POM if you don't want metal |  |  |  | https://www.amazon.com/Printer-Backlash-Threaded-Eliminate-Accessories/dp/B07XYQ4KJ9
Individual fastener list in case you need to source from elsewhere
M3, M4, M5 Nut and Screw Kit | 1 | $15.00 |  | https://www.amazon.com/Hilitchi-510-Pcs-Socket-Screws-Assortment/dp/B073SWXPYR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
M3 longer fastener kit | 1 | $9.28 |  | https://www.amazon.com/iexcell-Metric-M5-0-8-Stainless-Assortment/dp/B08GZWVN4D
M5 longer fastener kit | 1 | $9.80 |  | https://www.amazon.com/iexcell-Metric-M5-0-8-Stainless-Assortment/dp/B07HDL3KVG
Assorted M3 Kit | 1 | $12.00 |  | https://www.amazon.com/Kadrick-Bolts%EF%BC%8CFlat-Washers-Assortment-Stainless/dp/B0BPFWBBF9
M4x50 countersunk flat head | 4 | $2.00 |  | https://www.amazon.com/METALLIXITY-Countersunk-Machine-M4x30mm-Stainless/dp/B09Y5P7X75
M5x12 (M5x10 works too) button head | 100 | $0.10 |  | https://www.amazon.com/M5-0-8-Button-Socket-Stainless-Quantity/dp/B07NVJT9VB

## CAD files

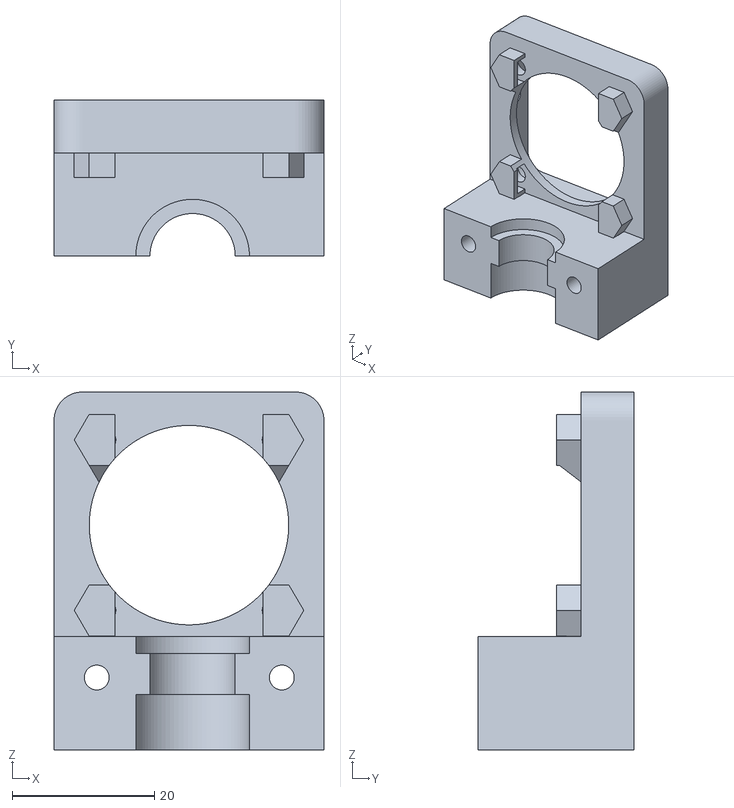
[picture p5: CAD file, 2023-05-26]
260/Gantry/V6 Front Mount x1 Coupler to Remain.stl
38.0 x 22.0 x 50.4

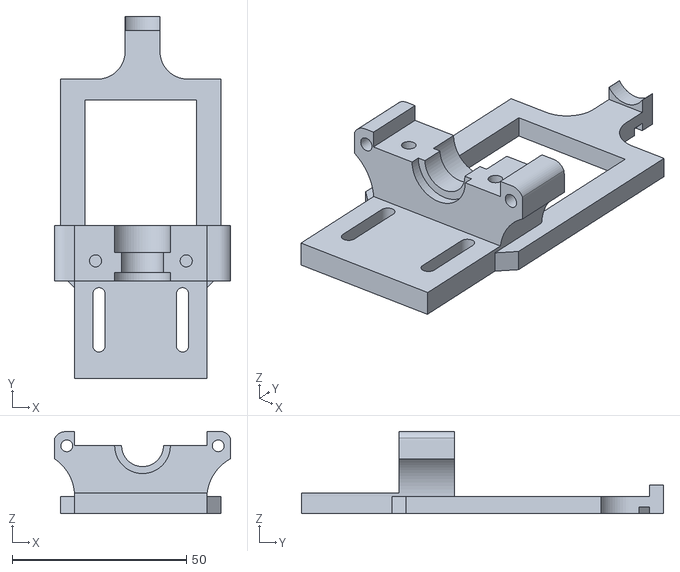
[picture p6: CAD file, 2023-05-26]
260/Gantry/V6 Back Mount x1 for coupler to remain.stl
50.6 x 104.0 x 23.7

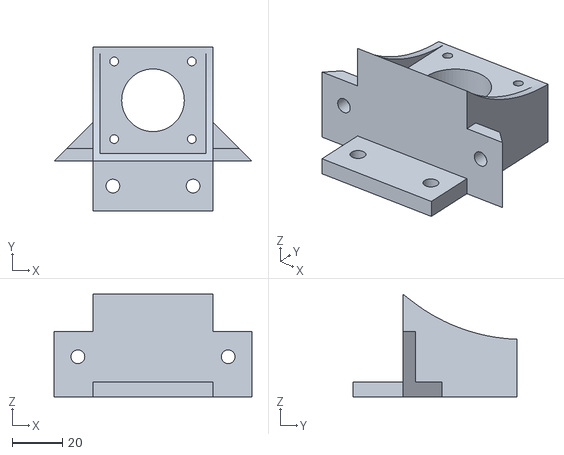
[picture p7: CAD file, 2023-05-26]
260/Bed and Z system/Z Motor Mount x1 supports build plate only.stl
79.1 x 65.6 x 41.0

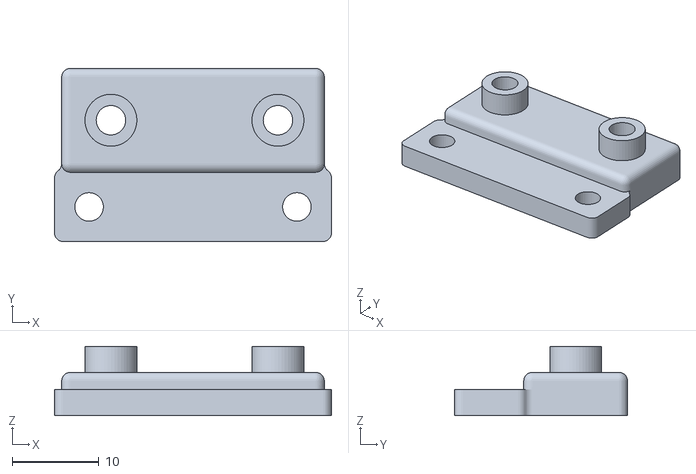
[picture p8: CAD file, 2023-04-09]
260/Electronics/ADXL Mount.stl
32.0 x 20.0 x 8.00

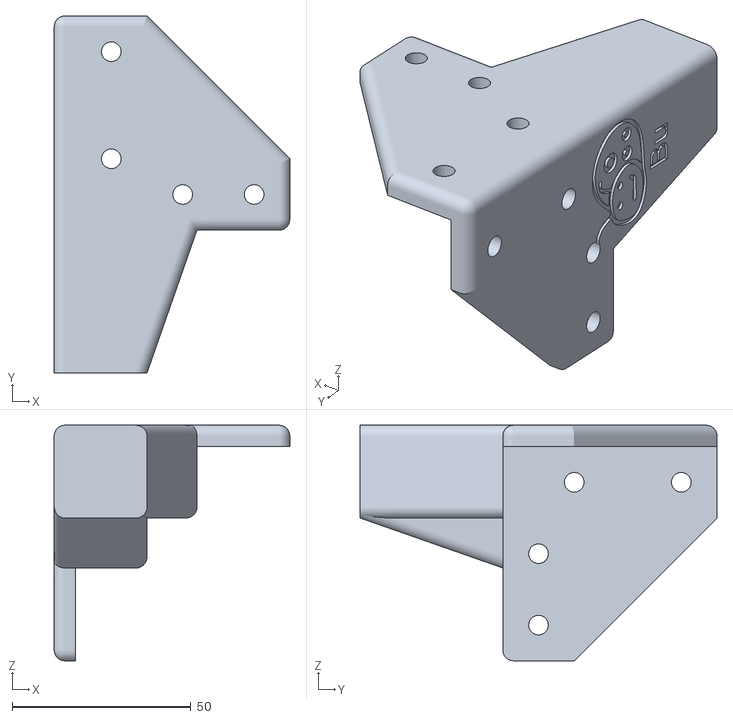
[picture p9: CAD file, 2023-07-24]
260/Main Frame Assembly/Foot FR & BL x2.stl
66.0 x 100.0 x 66.0

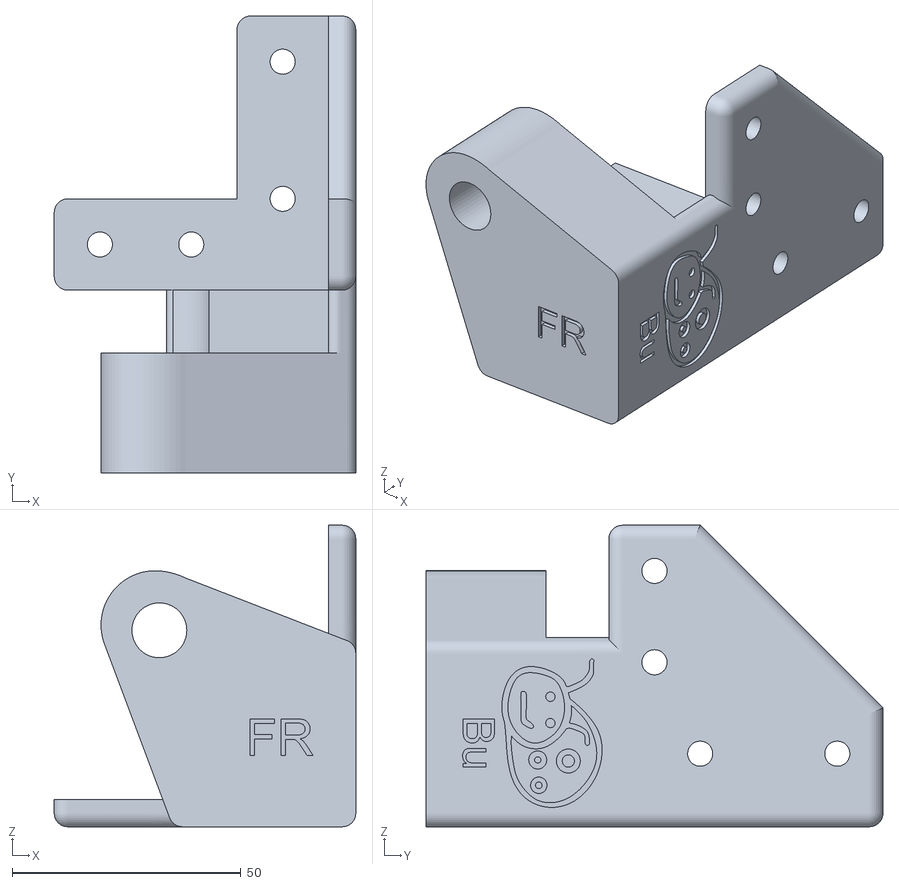
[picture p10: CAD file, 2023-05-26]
Mods/GoingTall/Foot_FR_for_Tall_x1.stl
66.0 x 100.0 x 66.0

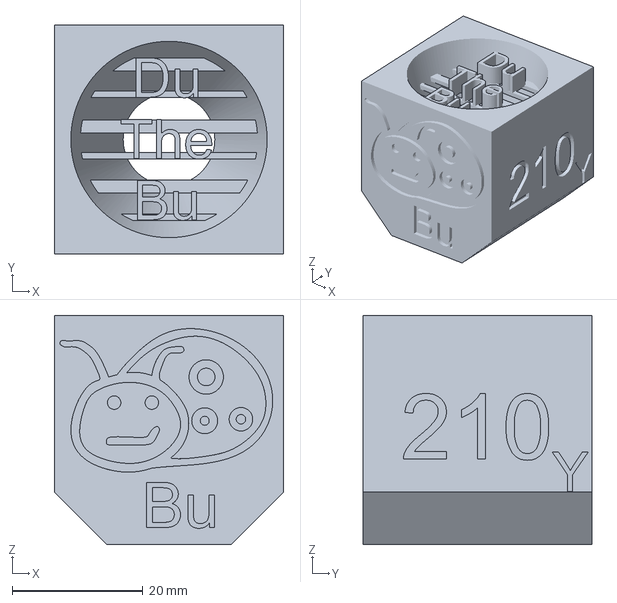
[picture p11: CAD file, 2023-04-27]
Slicer Configs/Bug Cube.3mf
35.0 x 35.0 x 35.0 mm

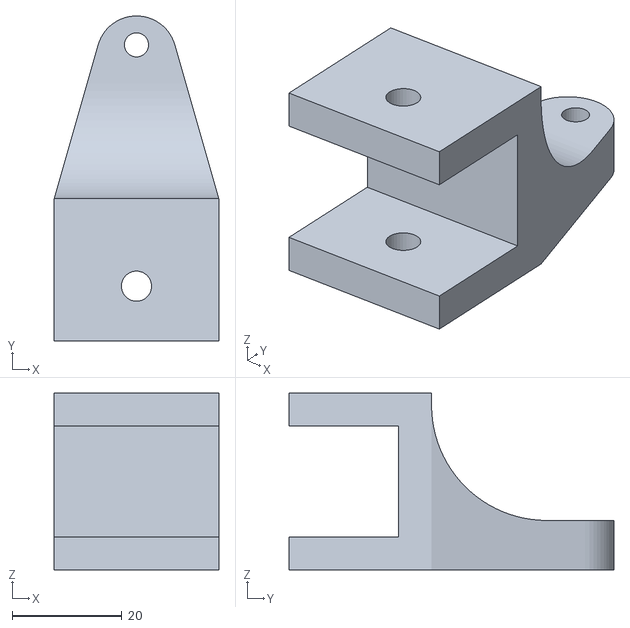
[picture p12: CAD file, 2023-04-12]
STL Files/Bed System/Alternate 310 Back Bed Mount x2 for using springs Print with Supports.stl
30.0 x 59.3 x 32.2

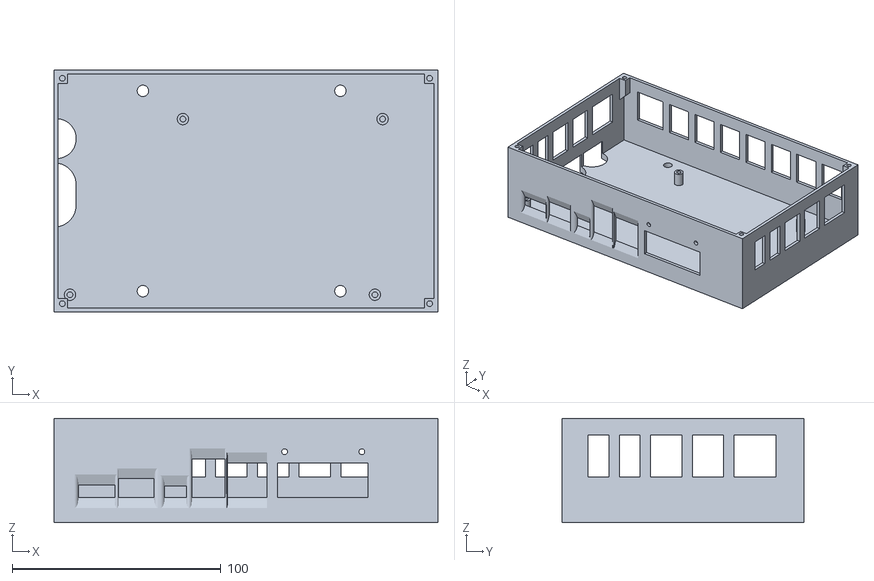
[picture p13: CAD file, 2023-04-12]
STL Files/Electronics/Manta_M4P/Manta M4P Backpack Case.stl
184.0 x 116.0 x 50.0

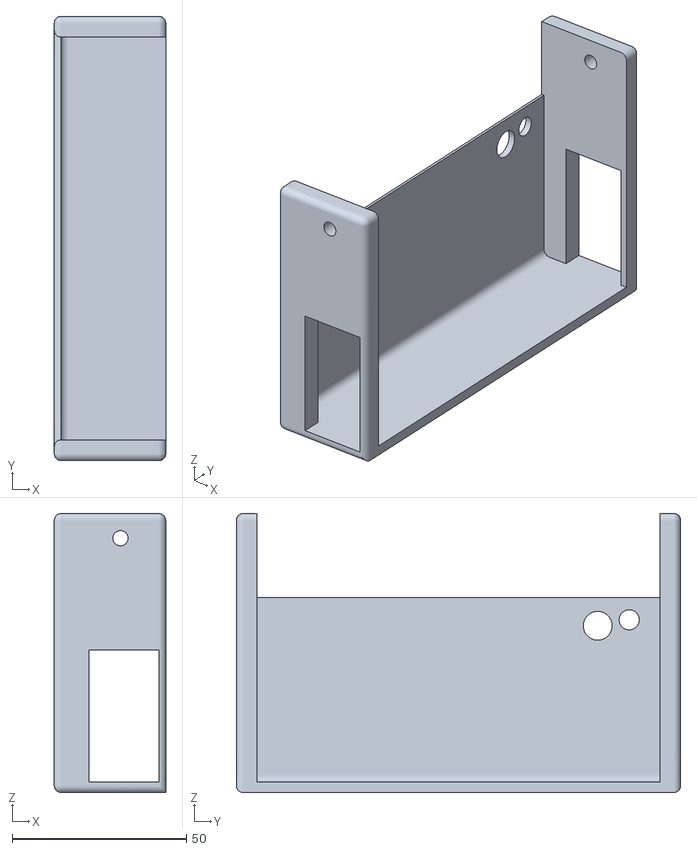
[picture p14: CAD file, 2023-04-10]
STL Files/Electronics/Meanwell 350 PSU Cover v1.stl
32.0 x 127.4 x 80.0

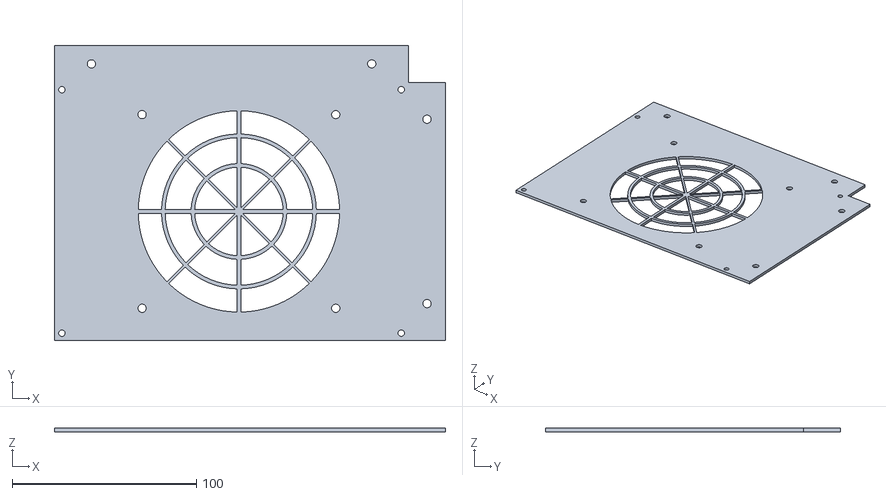
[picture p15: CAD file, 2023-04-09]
STL Files/Electronics/Octopus/Octopus V1.1 Lid option 1.stl
212.0 x 160.0 x 2.00

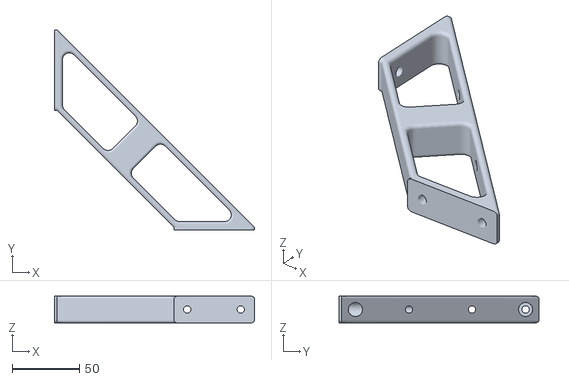
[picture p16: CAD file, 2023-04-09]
STL Files/Main Frame Assembly/Printed_Frame_Brace_x4.stl
149.2 x 149.2 x 20.0

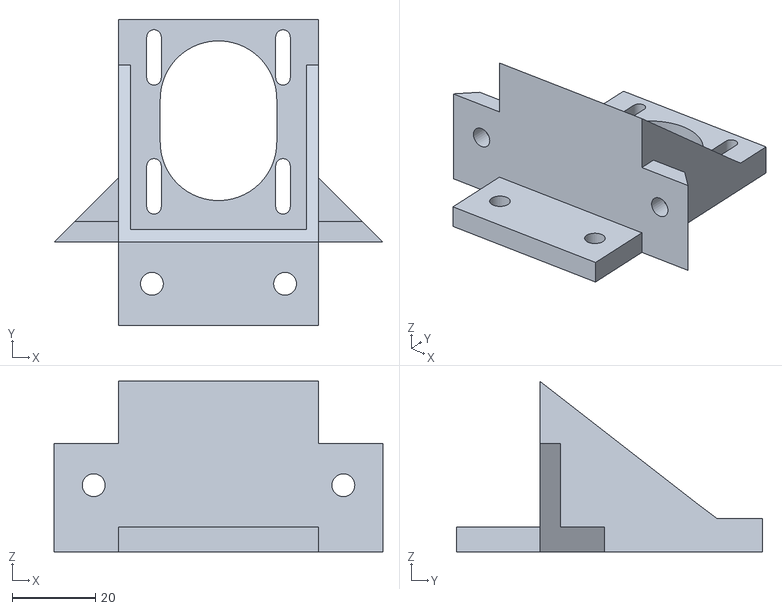
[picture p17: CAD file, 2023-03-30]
STL Files/Z System/Z - Motor Mount x1.stl
79.1 x 73.5 x 41.0

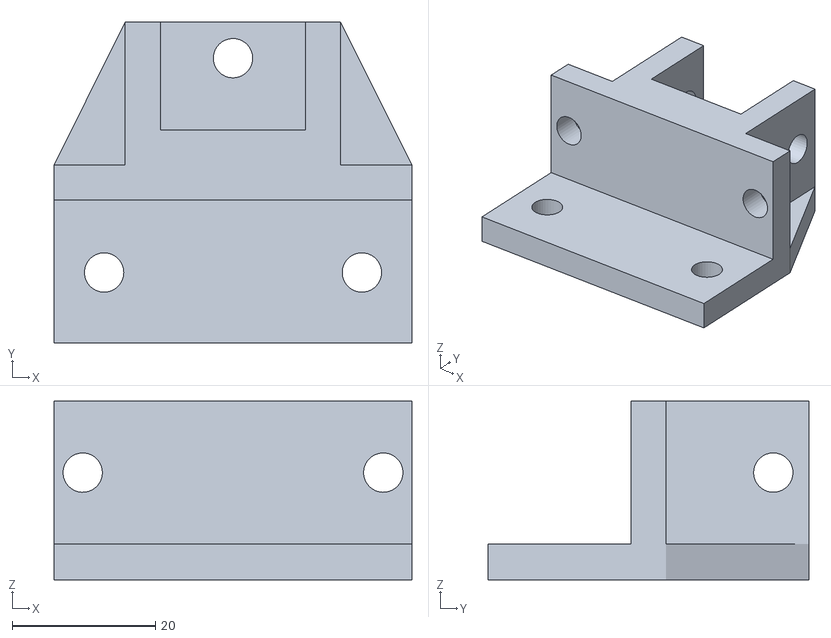
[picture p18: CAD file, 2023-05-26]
260/Bed and Z system/Bed Extrusion Bottom Tie x2.stl
50.0 x 44.9 x 25.0

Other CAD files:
260/Electronics/Gantry Cable Bundle Frame Tie x1.stl
260/Main Frame Assembly/Power Button in Foot OPTION.stl
Mods/GoingTall/Idler_FR_for_Tall_x1.stl
STL Files/Bed System/Alternate 310 FL Z Bed x1 for using springs.stl
260/Bed and Z system/Bed Extrusions Top Tie x2.stl
260/Bed and Z system/Cant Bed Mount Bracket x1.stl
260/Electronics/Electronics Backpack Case Lid.stl
260/Electronics/Electronics Backpack x1.stl
260/Electronics/PSU Cover x1.stl
260/Electronics/PSU Mount x2.stl
260/Electronics/Power Switch x1.stl
260/Gantry/BLtouch Mount x1.stl
260/Gantry/BugBu 5015 x1 use supports build plate only.stl
260/Gantry/GT2 Belt Clip x4.stl
260/Gantry/Gantry Clamp Left x1.stl
260/Gantry/Gantry Clamp Right x1.stl
260/Gantry/Gantry Primary Left x1.stl
260/Gantry/Gantry Primary Right x1.stl
260/Gantry/Hummingbird_extruder v1.stl
260/Gantry/Trihorn BugBu Duct x1.stl
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

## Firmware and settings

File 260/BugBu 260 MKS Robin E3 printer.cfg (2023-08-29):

[include mainsail.cfg]
[include Adaptive_Mesh.cfg]
#[include KAMP_Settings.cfg]
[exclude_object]
#[include PIS.cfg]
[include led_progress.cfg]

[virtual_sdcard]
path: ~/printer_data/gcodes

# This file contains common pin mappings for MKS Robin E3 boards. To
# use this config, the firmware should be compiled for the STM32F103.
# When running "make menuconfig", enable "extra low-level
# configuration setup", select the 20KiB bootloader, and serial (on
# USART1 PA10/PA9) communication.

# Note that the "make flash" command does not work with MKS Robin
# boards. After running "make", run the following command:
#   ./scripts/update_mks_robin.py out/klipper.bin out/Robin_e3.bin
# Copy the file out/Robin_e3.bin to an SD card and then restart the
# printer with that SD card.

# MKS Robin E3 has onboard TMC2209. This config can also be used for
# MKS Robin E3D if equipped with TMC2209 stepper drivers.

# Please note pin name change for stepper Z for v1.1 of the boards.

# See docs/Config_Reference.md for a description of parameters.

[stepper_x]
step_pin: PC0
dir_pin: !PB2
enable_pin: !PC13
microsteps: 16
rotation_distance: 40
endstop_pin: tmc2209_stepper_x:virtual_endstop
#endstop_pin: ^PA12
position_endstop: -5
position_min:-6
position_max: 245
homing_speed: 50
homing_retract_dist: 0

[stepper_y]
step_pin: PC2
dir_pin: !PB9
enable_pin: !PB12
microsteps: 16
rotation_distance: 40
endstop_pin: tmc2209_stepper_y:virtual_endstop
position_endstop: -5
position_min:-6
position_max: 235
homing_speed: 50
homing_retract_dist: 0

[stepper_z]
step_pin: PC14 # PC14 if using board v1.1
dir_pin: PC15 # !PC15 if using board v1.1
enable_pin: !PB8
microsteps: 16
rotation_distance: 8
endstop_pin: probe: z_virtual_endstop
position_max: 200
position_min: -10

[extruder]
max_extrude_only_distance: 400.0
step_pin: PB4
dir_pin: !PB3
enable_pin: !PB5
microsteps: 16
rotation_distance: 5.46
nozzle_diameter: 0.400
filament_diameter: 1.750
heater_pin: PC9
sensor_type: EPCOS 100K B57560G104F
sensor_pin: PA0
#control: pid
#pid_Kp: 21.527
#pid_Ki: 1.063
#pid_Kd: 108.982
min_temp: 0
max_temp: 250

[tmc2209 stepper_x]
uart_pin: PC7
run_current: 0.800
hold_current: 0.500
#stealthchop_threshold: 999999
diag_pin: ^PA12
driver_SGTHRS: 100 # 255 is most sensitive value, 0 is least sensitive

[tmc2209 stepper_y]
uart_pin: PD2
run_current: 0.800
hold_current: 0.500
#stealthchop_threshold: 999999
diag_pin: ^PA11
driver_SGTHRS: 110

[tmc2209 stepper_z]
uart_pin: PC12
run_current: 0.800
hold_current: 0.450
#stealthchop_threshold: 999999

[tmc2209 extruder]
uart_pin: PC11
run_current: 0.800
hold_current: 0.500
#stealthchop_threshold: 999999

[fan]
pin: PA8

[heater_bed]
heater_pin: PC8
sensor_type: EPCOS 100K B57560G104F
sensor_pin: PA1
#control: pid
# tuned for stock hardware with 50 degree Celsius target
#pid_Kp: 54.027
#pid_Ki: 0.770
#pid_Kd: 948.182
min_temp: 0
max_temp: 130

[bltouch]
sensor_pin: ^PB1
control_pin: PA3
pin_up_touch_mode_reports_triggered: False
probe_with_touch_mode: True
x_offset: -26
y_offset: -14
#z_offset: 0

[safe_z_home]
home_xy_position: 130, 115 # Change coordinates to the center of your print bed
speed: 50
z_hop: 10                 # Move up 10mm
z_hop_speed: 5

[bed_mesh]
speed: 300
horizontal_move_z: 5
mesh_min: 25, 25
mesh_max: 200, 200
probe_count: 5,5
algorithm: bicubic
fade_start: 1
fade_end: 10
fade_target: 0

#[filament_switch_sensor my_sensor]
#switch_pin: PB10
#...

[mcu]
serial: /dev/serial/by-id/usb-1a86_USB_Serial-if00-port0
restart_method: command

[printer]
kinematics: corexy
max_velocity: 500
max_accel: 2000      #Max 4000
max_z_velocity: 15        #Max 15 for 12V TMC Drivers, can increase for 24V
max_z_accel: 350
square_corner_velocity: 5.0

[neopixel my_led]
pin: PA2
chain_count: 32
# Use RGB values, must be between 0.0 and 0.1
initial_RED: 0.51
initial_GREEN: 0.0
initial_BLUE: 0.52


###########################################################################
## MACROS
###########################################################################


[gcode_macro _CLIENT_VARIABLE]
variable_use_custom_pos  : True  ; use custom park coordinates for x,y [True/False] 
variable_custom_park_x   : 200.0   ; custom x position; value must be within your defined min and max of X
variable_custom_park_y   : 210.0    ; custom y position; value must be within your defined min and max of Y
variable_custom_park_dz  : 2.0   ; custom dz value; the value in mm to lift the nozzle when move to park position 
variable_retract         : 1.0   ; the value to retract while PAUSE
variable_cancel_retract  : 5.0   ; the value to retract while CANCEL_PRINT
variable_speed_retract   : 35.0  ; retract speed in mm/s
variable_unretract       : 1.0   ; the value to unretract while RESUME
variable_speed_unretract : 35.0  ; unretract speed in mm/s
variable_speed_hop       : 15.0  ; z move speed in mm/s
variable_speed_move      : 120.0 ; move speed in mm/s
variable_park_at_cancel  : True  ; allow to move the toolhead to park while execute CANCEL_PRINT [True,False]
## !!! Caution [firmware_retraction] must be defined in the printer.cfg if you set use_fw_retract: True !!!
variable_use_fw_retract  : True  ; use fw_retraction instead of the manual version [True/False] 
gcode:


[gcode_macro UNLOAD_FILAMENT]
gcode:
 M83                   # Put the extruder into relative mode
 G92 E0.0              # Reset the extruder so that it thinks it is at position zero
 G1 E-350 F350          # Move the extruder backwards 350mm at a speed of 350mm/minute
 G92 E0.0              # Reset the extruder again
 M82                   # Put the extruder back into absolute mode.

[gcode_macro FILAMENT_LOAD]
gcode:
 M83                   # Put the extruder into relative mode
 G92 E0.0              # Reset the extruder so that it thinks it is at position zero
 G1 E350 F350          # Move the extruder forward 350mm at a speed of 350mm/minute
 G92 E0.0              # Reset the extruder again
 M82                   # Put the extruder back into absolute mode.

[gcode_macro M600]
description: Filament change
gcode: PAUSE X=10 Y=10 Z_MIN=50

[gcode_macro START_PRINT]
gcode:
  M104 S150 ; set temporary nozzle temp to prevent oozing during homing and auto bed leveling
  G4 S10 ; allow partial nozzle warmup
  {% set BED_TEMP = params.BED_TEMP|default(55)|float %}
  {% set EXTRUDER_TEMP = params.EXTRUDER_TEMP|default(220)|float %}
  M140 S{BED_TEMP} ; Start bed heating
  G90 ; Use absolute coordinates
  G28 ; Home all axes
  BED_MESH_CALIBRATE 
  BED_MESH_PROFILE LOAD=default
  G1 Z2.0 F3000 ; Move Z Axis up little to prevent scratching of Heat Bed
  G1 X2 Y20 Z30 F5000.0 ; Move to start position
  M190 S{BED_TEMP} ; Wait for bed to reach temperature
  M109 S{EXTRUDER_TEMP} ; Set and wait for nozzle to reach temperature
  G1 Z1.28 F240
  G92 E0
  G1 Y140 E10 F1500 ; prime the nozzle
  G1 X2.3 F5000
  G92 E0
  G1 Y10 E10 F1200 ; prime the nozzle
  G92 E0

[gcode_macro PID_EXTRUDER]
description: PID Tune for the Extruder
gcode:
  {% set TARGET_TEMP = params.TARGET_TEMP|default(220)|float %} 
  PID_CALIBRATE HEATER=extruder TARGET={TARGET_TEMP}
  TURN_OFF_HEATERS
  SAVE_CONFIG

[gcode_macro PID_BED]
description: PID Tune for the Bed
gcode:
  {% set TARGET_TEMP = params.TARGET_TEMP|default(70)|float %} 
  PID_CALIBRATE HEATER=heater_bed TARGET={TARGET_TEMP}
  TURN_OFF_HEATERS
  SAVE_CONFIG

#[gcode_macro G29]				
gcode:
  G28
  bed_mesh_calibrate
  G1 X0 Y0 Z10 F4200

[Pause_Resume]
recover_velocity: 25

[gcode_macro Set_Z_Offset]
description: start process because I'm forgetful 
gcode:
    G28
    probe_calibrate

[gcode_macro PRIME_LINE]
gcode:
    M117 Prime Line
    G92 E0 ;Reset Extruder
    # move z axis
    G1 Z2.0 F3000 ;Move Z Axis up
    # move to prime position
    G1 X10 Y30 Z0.4 F5000.0 ;Move to start position
    G1 X10 Y200.0 Z0.4 F1500.0 E15 ;Draw the first line
    G1 X11 Y200.0 Z0.4 F5000.0 ;Move to side a little
    G1 X11 Y30 Z0.4 F1500.0 E30 ;Draw the second line
    #G1 E-0.2
    G92 E0 ;Reset Extruder
    G1 Z2.0 F3000 ;Move Z Axis up

#*# <---------------------- SAVE_CONFIG ---------------------->
#*# DO NOT EDIT THIS BLOCK OR BELOW. The contents are auto-generated.
#*#
#*# [extruder]
#*# control = pid
#*# pid_kp = 26.184
#*# pid_ki = 1.800
#*# pid_kd = 95.243
#*#
#*# [heater_bed]
#*# control = pid
#*# pid_kp = 70.540
#*# pid_ki = 1.274
#*# pid_kd = 976.102
#*#
#*# [bltouch]
#*# z_offset = 2.160
#*#
#*# [bed_mesh default]
#*# version = 1
#*# points =
#*# 	-0.440000, -0.687500, -0.950000, -1.267500, -1.625000
#*# 	-0.042500, -0.262500, -0.507500, -0.767500, -1.097500
#*# 	0.372500, 0.157500, -0.057500, -0.297500, -0.565000
#*# 	0.837500, 0.670000, 0.500000, 0.302500, 0.040000
#*# 	1.347500, 1.232500, 1.062500, 0.895000, 0.667500
#*# x_count = 5
#*# y_count = 5
#*# mesh_x_pps = 2
#*# mesh_y_pps = 2
#*# algo = lagrange
#*# tension = 0.2
#*# min_x = 25.0
#*# max_x = 200.0
#*# min_y = 25.0
#*# max_y = 200.0

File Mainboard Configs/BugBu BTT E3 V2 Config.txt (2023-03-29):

# This file contains common pin mappings for the BIGTREETECH SKR mini
# E3 v2.0. To use this config, the firmware should be compiled for the
# STM32F103 with a "28KiB bootloader" and USB communication. Also,
# select "Enable extra low-level configuration options" and configure
# "GPIO pins to set at micro-controller startup" to "!PA14".

# The "make flash" command does not work on the SKR mini E3. Instead,
# after running "make", copy the generated "out/klipper.bin" file to a
# file named "firmware.bin" on an SD card and then restart the SKR
# mini E3 with that SD card.

# See docs/Config_Reference.md for a description of parameters.


[mcu]
##  Obtain definition by "ls -l /dev/serial/by-id/" then unplug to verify
##--------------------------------------------------------------------
serial: /dev/serial/by-id/usb-Klipper_stm32f103xe_39FFD7053041543708752343-if00
restart_method: command
##--------------------------------------------------------------------

[printer]
kinematics: corexy
max_velocity: 500
max_accel: 30000             #Max 4000
max_z_velocity: 15          #Max 15 for 12V TMC Drivers, can increase for 24V
max_z_accel: 350
square_corner_velocity: 5.0

[stepper_x]
step_pin: PB13
dir_pin: PB12
enable_pin: !PB14
microsteps: 64
rotation_distance: 40
endstop_pin: tmc2209_stepper_x:virtual_endstop
position_endstop: 0
position_max: 215
homing_speed: 40
homing_retract_dist: 0

[tmc2209 stepper_x]
uart_pin: PC11
tx_pin: PC10
uart_address: 0
run_current: 0.8
#sense_resistor: 0.110
stealthchop_threshold: 0
interpolate: False
diag_pin: ^PC0    # Set to MCU pin connected to TMC DIAG pin
driver_SGTHRS: 90 # 255 is most sensitive value, 0 is least sensitive

[stepper_y]
step_pin: PB10
dir_pin: PB2
enable_pin: !PB11
microsteps: 64
rotation_distance: 40
endstop_pin: tmc2209_stepper_y:virtual_endstop
position_endstop: 0
position_max: 200
homing_speed: 40
homing_retract_dist: 0

[tmc2209 stepper_y]
uart_pin: PC11
tx_pin: PC10
uart_address: 2
run_current: 0.8
#sense_resistor: 0.110
stealthchop_threshold: 0
interpolate: False   # Set to MCU pin connected to TMC DIAG pin
diag_pin: ^PC1
driver_SGTHRS: 110

[stepper_z]
step_pin: PB0
dir_pin: PC5
enable_pin: !PB1
microsteps: 64
rotation_distance: 8
# endstop_pin: ^PC2
# position_endstop: 0.0
endstop_pin: probe:z_virtual_endstop
position_max: 200
position_min: -10

[tmc2209 stepper_z]
uart_pin: PC11
tx_pin: PC10
uart_address: 1
run_current: 0.8
#hold_current: 0.75
stealthchop_threshold: 999999

[extruder]
step_pin: PB3
dir_pin: !PB4
enable_pin: !PD2
microsteps: 16
rotation_distance: 4.32
nozzle_diameter: 0.400
filament_diameter: 1.750
heater_pin: PC8
sensor_type: EPCOS 100K B57560G104F
sensor_pin: PA0
#control: pid
#pid_Kp: 21.527
#pid_Ki: 1.063
#pid_Kd: 108.982
min_temp: 0
max_temp: 250
max_extrude_only_distance: 101
pressure_advance: 0.0

[tmc2209 extruder]
uart_pin: PC11
tx_pin: PC10
uart_address: 3
run_current: 0.650
stealthchop_threshold: 999999

[heater_bed]
heater_pin: PC9
sensor_type: ATC Semitec 104GT-2
sensor_pin: PC3
#control: pid
#pid_Kp: 54.027
#pid_Ki: 0.770
#pid_Kd: 948.182
min_temp: 0
max_temp: 130

[heater_fan heatbreak_cooling_fan]
pin: PC6

[fan]
pin: PC7

[static_digital_output usb_pullup_enable]
pins: !PA14

[board_pins]
aliases:
    # EXP1 header
    EXP1_1=PB5,  EXP1_3=PA9,   EXP1_5=PA10, EXP1_7=PB8,  EXP1_9=<GND>,
    EXP1_2=PA15, EXP1_4=<RST>, EXP1_6=PB9,  EXP1_8=PB15, EXP1_10=<5V>

# See the sample-lcd.cfg file for definitions of common LCD displays.

[safe_z_home]
home_xy_position: 100,100 # Change coordinates to the center of your print bed
speed: 50
z_hop: 10                 # Move up 10mm
z_hop_speed: 5

[bed_mesh]
speed: 120
horizontal_move_z: 5
mesh_min: 5, 10
mesh_max: 160, 160
probe_count: 3, 3

[bltouch]
stow_on_each_sample: False
probe_with_touch_mode: True
sensor_pin: ^PC14
control_pin: PA1
x_offset: -28
y_offset: -16
#z_offset: 3.0
speed: 5




[include macros.cfg]

[exclude_object]

[include fluidd.cfg]

#*# <---------------------- SAVE_CONFIG ---------------------->
#*# DO NOT EDIT THIS BLOCK OR BELOW. The contents are auto-generated.
#*#
#*# [bed_mesh default]
#*# version = 1
#*# points =
#*# 	  0.071875, 0.013125, 0.033750
#*# 	  0.211875, 0.143125, 0.085000
#*# 	  0.158750, 0.081250, 0.039375
#*# x_count = 3
#*# y_count = 3
#*# mesh_x_pps = 2
#*# mesh_y_pps = 2
#*# algo = lagrange
#*# tension = 0.2
#*# min_x = 5.0
#*# max_x = 160.0
#*# min_y = 10.0
#*# max_y = 160.0
#*#
#*# [heater_bed]
#*# control = pid
#*# pid_kp = 66.575
#*# pid_ki = 1.268
#*# pid_kd = 873.796
#*#
#*# [extruder]
#*# control = pid
#*# pid_kp = 30.179
#*# pid_ki = 3.796
#*# pid_kd = 59.981
#*#
#*# [bltouch]
#*# z_offset = 3.595

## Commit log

2023-01-30 BugBu CAD
    BugBu Step File
2023-01-30 CAD
    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
2023-03-06 Pending changes exported from your codespace
    [BC Z to Bed Clamp x1.stl, BC Z to Bed x1.stl, BLtouch Mount x1.stl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]
2023-03-07 Added mainboard config, slicer config, and Images
    [BC Z to Bed Clamp x1.stl, BC Z to Bed x1.stl, BLtouch Mount x1.stl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]
2023-03-08 git config pull.rebase false
    [Bugbu 300 BOM.xlsx, Hummingbird_extruder_v1.stl]
2023-03-11 Adjusted to Use M5x25 instead of M5x40
    [Z - Belt Tensioner Long x1.stl]
2023-03-12 Fixed Extrusion Qauntities in BOM
    [Bugbu 300 BOM.xlsx]
2023-03-16 Updated mainboard instructions
    [BugBu BTT E3V3 Config.txt]
2023-03-16 Updated config for BTT E3V3
    [BugBu BTT E3V3 Config.txt]
2023-03-22 Added Power Switch, Renamed to Printable Area
    [Bugbu 210 BOM.xlsx]
2023-03-23 Individual Parts Cad
2023-03-23 Updated Fasteners on list
    [Bugbu 210 BOM.xlsx]
2023-03-29 Config Contributed by Matts3DP
    [BugBu BTT E3 V2 Config.txt]
2023-03-30 Made mountable using M5x12 to standardize build
    [Bed Strain Relief x1.stl, Electronics Backpack x1.stl, Z - Motor Mount x1.stl]
2023-03-30 Added frame bracket for gantry wiring
    [Gantry Cable Bundle Frame Tie x1.stl]
2023-04-09 File Reorg, 310 Additions, Moar Backpacks
    [210 FL Z to Bed x1.stl, 210 FR Z to Bed x1.stl, 310_Back_Bed_Mount_x2_Print_with_Supports.stl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]
2023-04-10 Added cover for Meanwell 350 PSU
    If you choose to use a Meanwell over the BOM PSU, use this stl.
    [Meanwell 350 PSU Cover v1.stl]
2023-04-12 Fixed case openings
    [Manta M4P Backpack Case.stl]
2023-04-12 Added 310 Bed Mounts for using bed springs
    [310 Back Bed Mount x2 for using springs Print with Supports.stl, 310 FL Z Bed x1 for using springs.stl, 310 FR Z Bed x1 for using springs.stl]
2023-04-12 alternate 310 bed mounts to use bed springs
    [Alternate 310 Back Bed Mount x2 for using springs Print with Supports.stl, Alternate 310 FL Z Bed x1 for using springs.stl, Alternate 310 FR Z Bed x1 for using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]
2023-04-27 Added 3MF files for Orca Config
    [Bug Cube.3mf]
2023-05-01 Fixed M3 captured and added reinforcement area
    [V6 Front Mount x1 with supports build plate only.stl]
2023-05-26 GoingTall Mods By Rolls, tested by Frankenbee
    [310 Back Bed Mount x2 for using springs Print with Supports.stl, FL Z to Bed for Tall x1 v1.stl, FL_Bottom_Frame_x1.stl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]
2023-05-26 Bugbu 260 Files
    [ADXL Mount.stl, BLtouch Mount x1.stl, Bed Extrusion Bottom Tie x2.stl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]
2023-07-10 Updated to fix linear rod lengths
    [Bugbu 260 BOM.xlsx]
2023-07-24 Fixed BugBu one Feet
    [Foot FR & BL x2.stl, Foot FL & BR x2.stl]
2023-08-29 MKS Robin E3 Printer Config
    [BugBu 260 MKS Robin E3 printer.cfg]
2024-03-09 Axle Drive parts STEP files
